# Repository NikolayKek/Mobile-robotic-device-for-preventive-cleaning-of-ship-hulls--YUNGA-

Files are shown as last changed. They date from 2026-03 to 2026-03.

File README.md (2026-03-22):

# Функциональная модель мобильного роботизированного устройства для профилактической чистки судовых корпусов от органических обрастаний «ЮНГА»
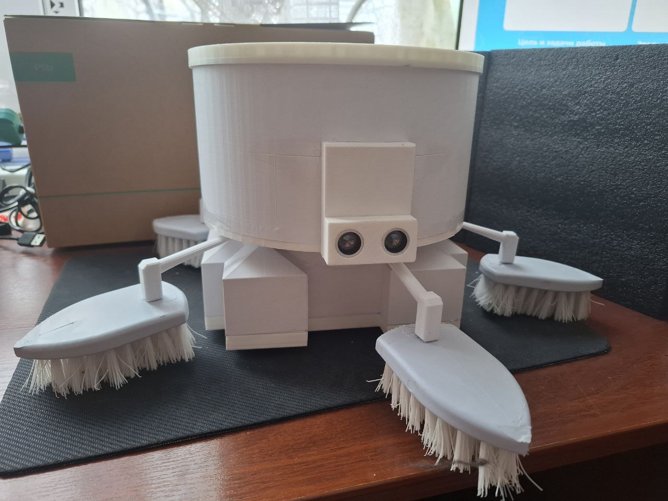
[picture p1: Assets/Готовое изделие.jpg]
Готовое изделие
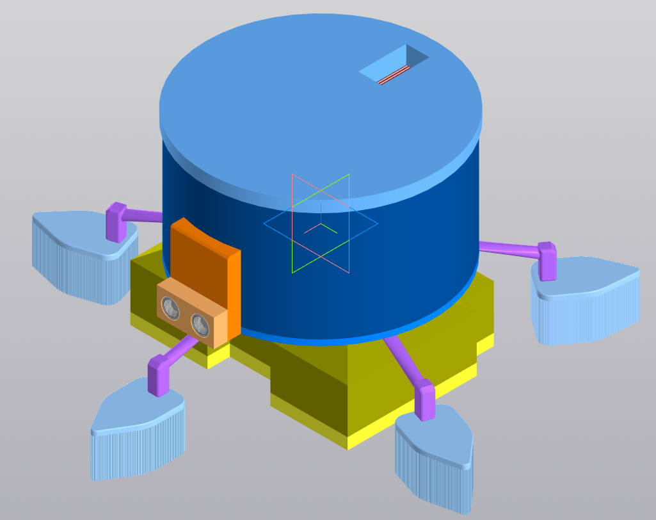
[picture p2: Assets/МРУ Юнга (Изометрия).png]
МРУ Юнга (Изометрия)
  

## Цель создания МРУ Юнга: 
Cпроектировать и изготовить модель мобильного роботизируемого устройства для профилактической чистки корпуса судна от органических обрастаний, без необходимости его постановки в док, которая будет производиться во время стоянки судна или на рейде (на малой скорости или дрейфе) силами экипажа, для оптимизации расходов на содержание судна.

## Задачи проекта: 
- Проанализировать основные методы борьбы с обрастанием  
- Проанализировать типы очистки корпуса корабля  
- Изучить используемые для очистки от обрастаний РУ. 
- Оценить эффективность МРУ.  
- Создать общую концепцию модели. 
- Создать чертеж устройства. 
- Выбрать материалы и комплектующие изделия. 
- Напечатать детали устройства на 3D-принтере. 
- Собрать устройство. 
- Запрограммировать устройство.
- Проверить работу устройства.  

## Общая концепция модели:
Технически МРУ представляет собой мобильную автоматизированную конструкцию, которая крепится на поверхности корпуса судна и перемещается по ней, удаляя грязь и обрастателей. Устройство предназначено для профилактической чистки, которая осуществляется за счет трения щёток о поверхность корпуса судна. 
Электрический двигатель создает и постоянно поддерживает вакуум, за счет которого устройство притягивается корпусу. Одновременно с притяжением происходит перемещение робота по поверхности и удаление загрязнений и прикрепившихся обрастателей. Робот передвигается с помощью треков (гусениц), изготовленных из резины, которые не повреждают поверхность корпуса.  
Питание робота осуществляется при постоянном подключении к электросети судна. Этот метод подачи энергии гарантирует стабильную и бесперебойную работу всех его систем, исключая необходимость в регулярной подзарядке или замене элементов питания. Резервным питанием робота служит аккумулятор. 
МРУ также снабжено стальным страховочным тросом.

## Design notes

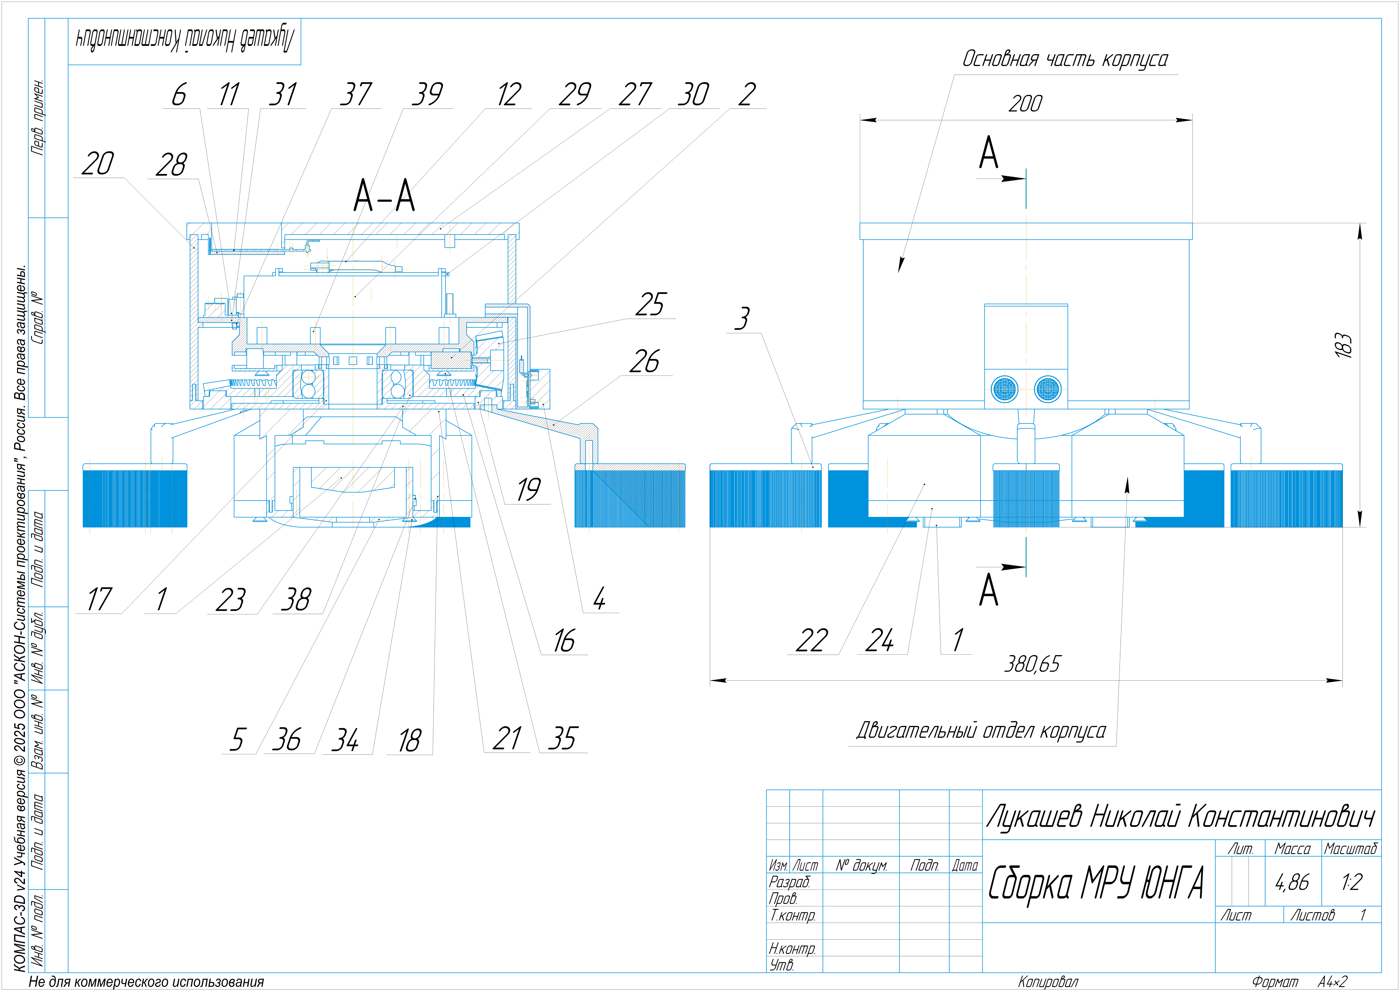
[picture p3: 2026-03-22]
Чертёж, спецификация и приложения/Чертёж сборки/Чертёж сборки МРУ.png

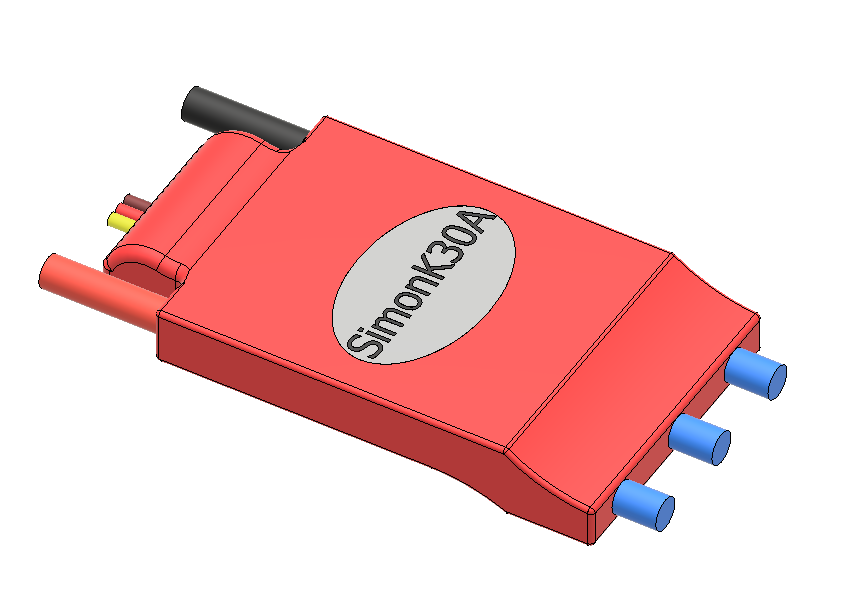
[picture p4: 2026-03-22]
3D модели/В. детали/Для ESC регулятора 30A с прошивкой SimonK/SimonK30A.png

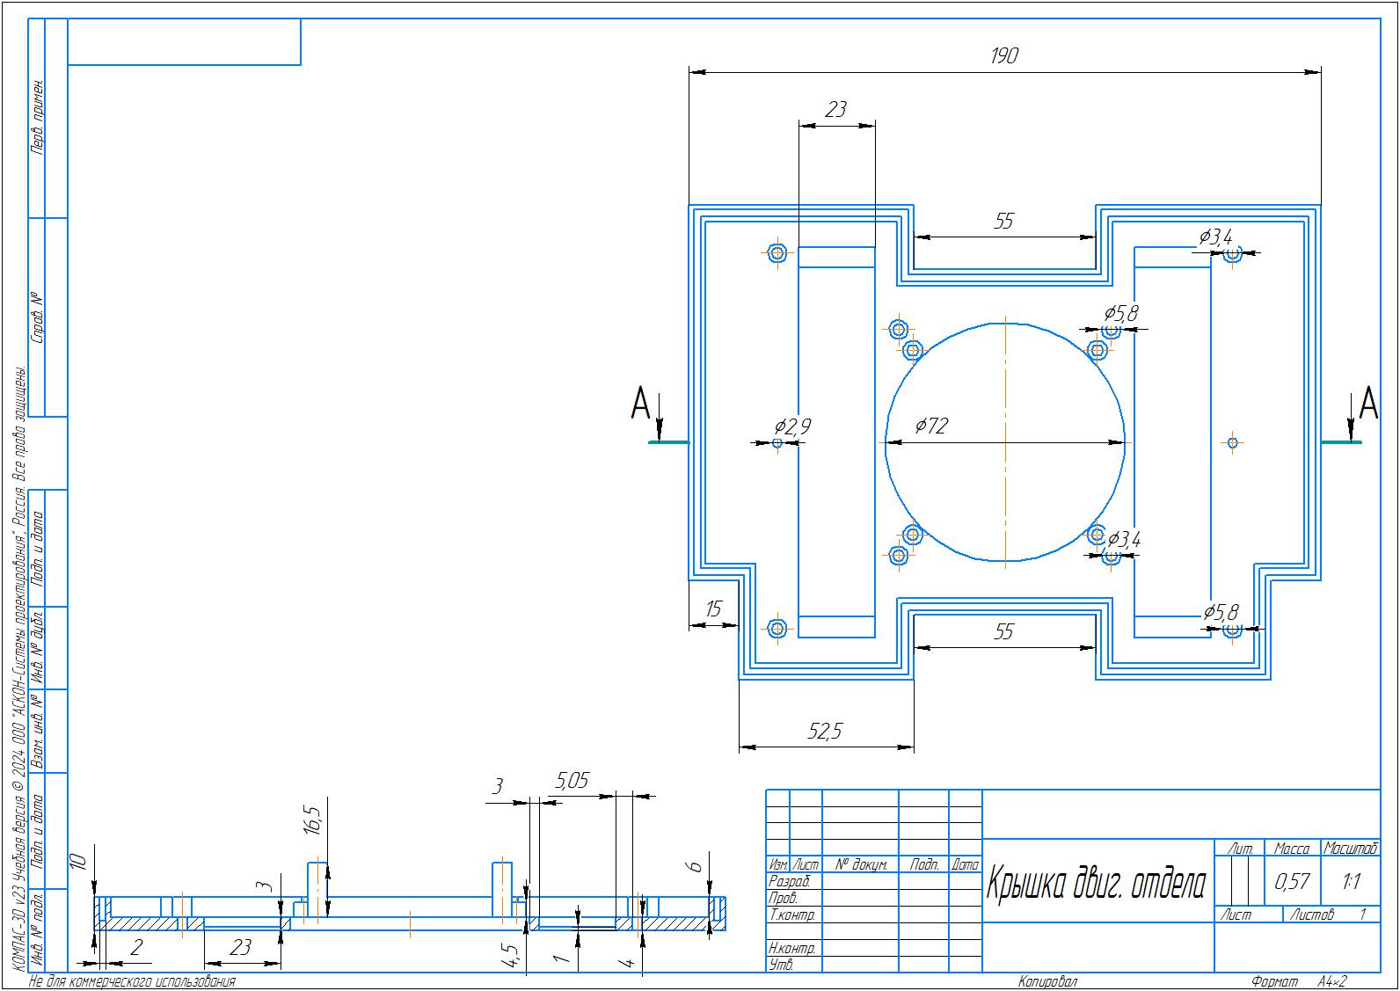
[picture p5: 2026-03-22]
3D модели/Двигательный отдел/Изображения/Крышка двиг. отдела.jpg

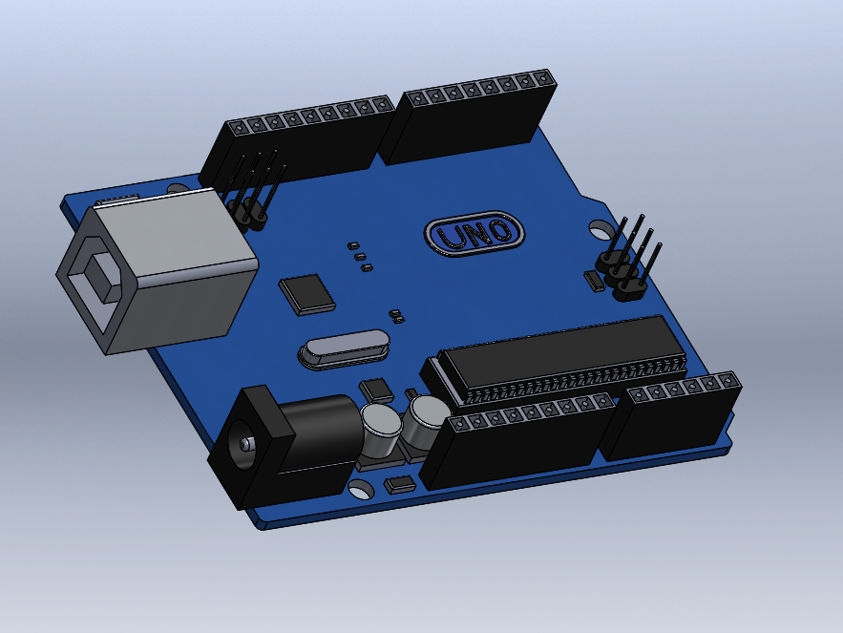
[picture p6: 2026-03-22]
3D модели/В. детали/Для Arduino Uno R3/Arduino Uno R3.PNG

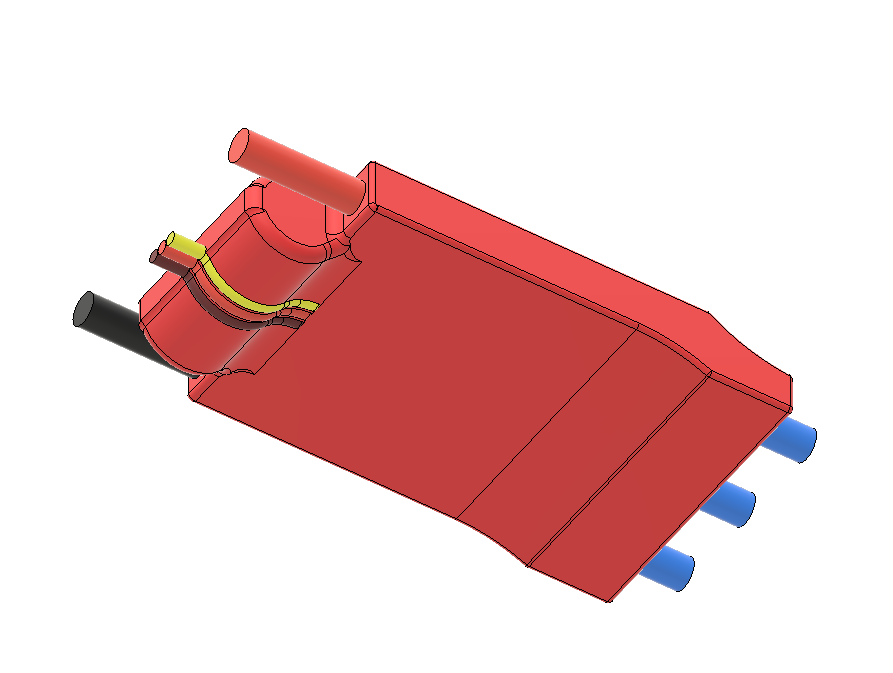
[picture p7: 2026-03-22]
3D модели/В. детали/Для ESC регулятора 30A с прошивкой SimonK/SimonK30A 3.png

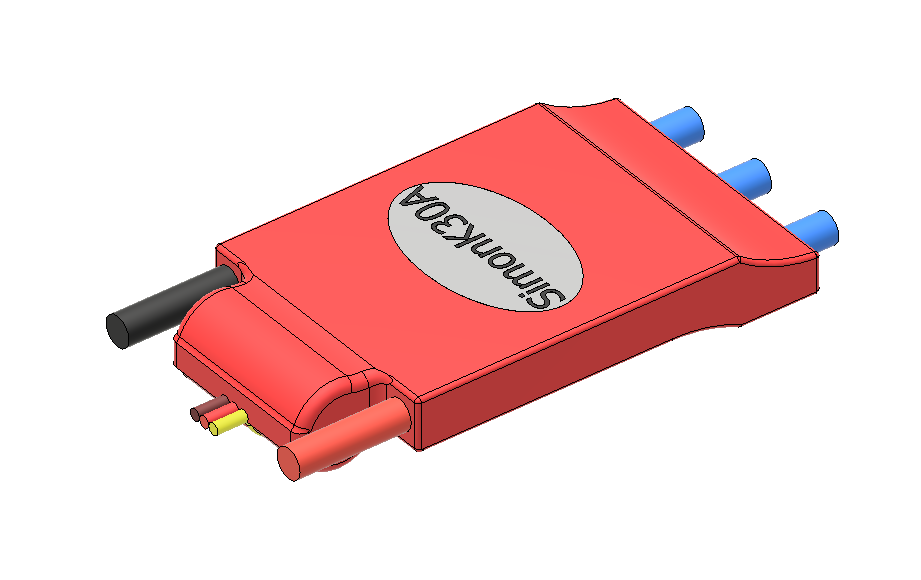
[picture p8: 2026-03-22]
3D модели/В. детали/Для ESC регулятора 30A с прошивкой SimonK/SimonK30A 2.png

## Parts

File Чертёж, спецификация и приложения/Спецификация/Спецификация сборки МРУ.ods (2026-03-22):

Формат | Зона | Поз. | Обозначение | Наименование | Кол. | Приме- чание | Масса | БЦО | Обозн_СТ | Вид изделия | ID ФГ | ID PartLib | Код ОКП | ID материала | Обозначение материала
 |  |  |  | Сборочные единицы
 |  | 1 | $|-$|01$|$|$|$| | Двигатель R-385-18915-3 24V | 2 |  | 0.06
 |  | 2 |  | Мотор - редуктор N20 6V | 3 |  | 0.015
 |  | 3 |  | Щётка | 5 |  | 0.1
 |  | 4 |  | Модуль ультразвукового датчика | 1 |  | 0.028306
 |  | 5 |  | Вакуумный двигатель BL2717 | 1 |  | 0.18
 |  | 6 |  | DC-DC XL6009 | 1 |  | 0.015
 |  | 7 |  | ARDUINO UNO R3 | 1 |  | 0.025
 |  | 8 |  | Aleaivy 3S2P 18650 12В 7000мАч | 1 |  | 0.45
 |  | 9 |  | Amperka Troyka Shield | 1 |  | 0.012
 |  | 10 |  | Amperka Motor Shield L298P | 1 |  | 0.015
 |  | 11 |  | Датчик уровня воды | 1 |  | 0.003
 |  | 12 |  | 30A ESC SimonK Firmware | 1 |  | 0.045
 |  | 13 |  | Реле TRU-5VDC | 1 |  | 0.025
 |  |  |  | Детали
 |  | 16 |  | Шестерня ведомая | 1 |  | 0.107621
 |  | 17 |  | Втулка для подшипника | 1 |  | 0.008976
 |  | 18 |  | Рама для моторов | 1 |  | 0.04811
 |  | 19 |  | Держатель стержней щёток | 1 |  | 0.07984
 |  | 20 |  | Корпус МРУ | 1 |  | 0.276945
 |  | 21 |  | Нижние пазы основной части корпуса МРУ | 1 |  | 0.034244
 |  | 22 |  | Корпус двигательного отдела | 1 |  | 0.282968
 |  | 23 |  | Нижняя часть рамы | 1 |  | 0.050972
@100~) |  | 24 |  | Крышка двигательного отдела | 1 | @100~)A4@4~2 | 0.072419
 |  | 25 |  | Шестерня ведущая | 3 |  | 0.010107
 |  | 26 |  | Стержень для щётки | 5 |  | 0.004759
 |  | 27 |  | Крышка основной части корпуса | 1 |  | 0.223097
 |  | 28 |  | Крышка для датчика воды | 1 |  | 0.002565
 |  | 29 |  | Кейс для аккумуляторный батареи | 1 |  | 0.02469
 |  | 30 |  | Крышка для кейса для аккумуляторной батареи | 1 |  | 0.013936
 |  | 31 |  | Верхняя часть рамы | 1 |  | 0.154037
 |  |  |  | Стандартные изделия
 |  | 34 |  | Countersunk flat head screw ISO 7046-1 - М4 x 20 - H | 6 |  | 0.002 |  |  |  |  | BOSimple***PART:4a2be23b-1094-c2ab-9109-1eb2c62276f1***SHORTLOC:A259_B079D7FF98134C2D[H;0,7;20;4;-;Undefined] |  |  | Сталь 10 ГОСТ 1050-2013
 |  | 35 |  | Countersunk flat head screw ISO 7046-1 - М4 x 25 - Z | 8 |  | 0.00239 |  |  |  |  | BOSimple***PART:92ec0e0d-68d0-4f9e-eaa2-c9b13db8eb2e***SHORTLOC:A259_B079D7FF98134C2D[Z;0,7;25;4;-;Undefined] |  |  | Сталь 10 ГОСТ 1050-2013
 |  | 36 |  | Hexagon thin nut ISO 4035 - М4 | 4 |  | 0.000561 |  |  |  |  | BOSimple***PART:b6312abf-3635-9e75-d080-44536a865479***SHORTLOC:A259_4C5EF5FF3D3C4192[0,7;4;7;-;Undefined] |  |  | Сталь 10 ГОСТ 1050-88
 |  | 37 |  | Винт 2-3x1x10.12 ГОСТ 10619-80 | 4 |  | 0.00046 |  |  |  |  | BOSimple***PART:a135eb40-4c64-62b3-542c-7c3df5bf31bf***SHORTLOC:A86A9_F1ECDF2721C54B79[Нет;Без покрытия;3;10;1;Сталь 30ХГСА ГОСТ 4543-2016] |  | BOSimple***Material:a0aec22f-052f-4fdd-a19d-c95e78cbd053 | Сталь 30ХГСА ГОСТ 4543-2016
 |  | 38 |  | Подшипник 1207 ГОСТ 28428-90 | 1 |  | 0.323 |  |  |  |  | BOSimple***PART:c0ee8c61-a45f-0a07-f1a0-e0ef849b54f1***SHORTLOC:AFFB_506398E62AE44C9C[35;72;17] |  |  | Сталь 10 ГОСТ 1050-88
 |  | 39 |  | Резьбовая втулка | 10 |  | 0.001234

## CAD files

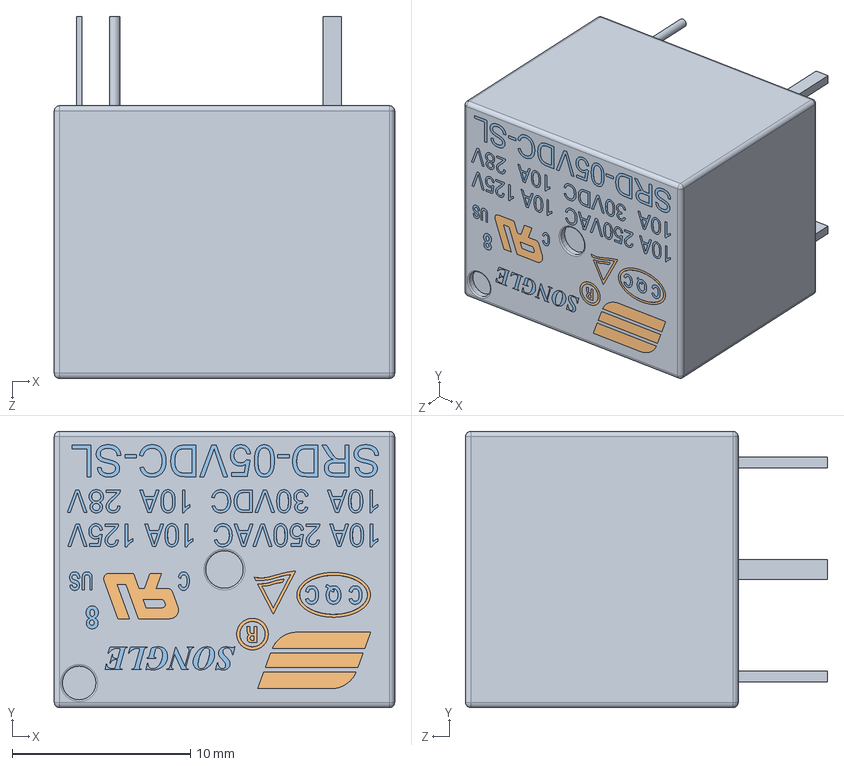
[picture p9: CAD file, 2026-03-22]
3D модели/В. детали/Для реле TRU-5VDC/relay_songle_asm.SLDASM
19.1 x 15.5 x 20.3 mm
Relay SPDT Songle
logos
texts

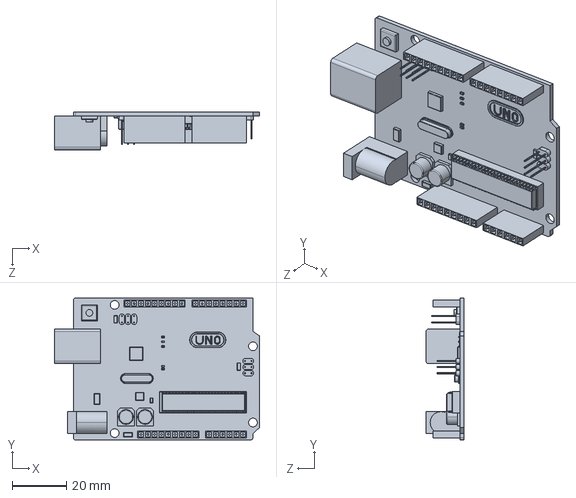
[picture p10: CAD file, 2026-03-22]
3D модели/В. детали/Для Arduino Uno R3/ARDUINO UNO R3 Step.STEP
75.3 x 52.1 x 13.9 mm

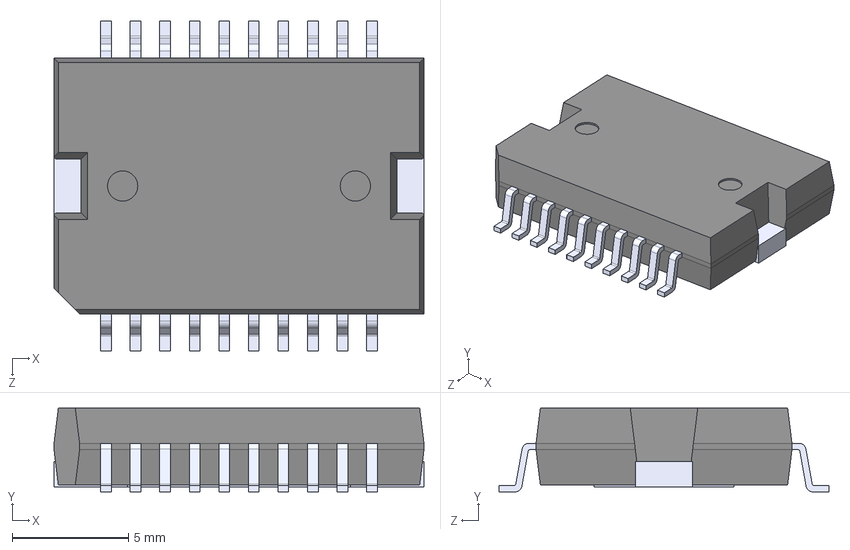
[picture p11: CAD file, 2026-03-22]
3D модели/В. детали/Для драйвера моторов Amperka Motor Shield/L298P_SO20_MODEL.STEP
15.9 x 3.60 x 14.2 mm

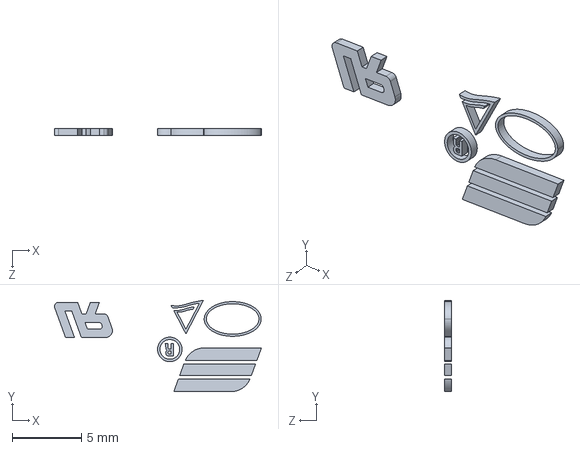
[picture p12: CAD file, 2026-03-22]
3D модели/В. детали/Для реле TRU-5VDC/logos.SLDPRT
15.0 x 6.61 x 0.5 mm

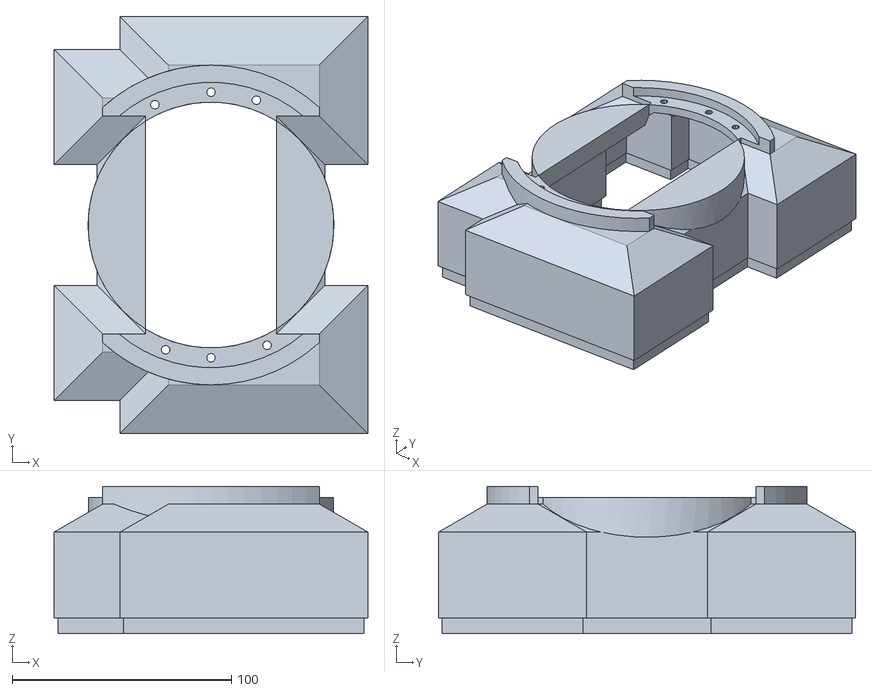
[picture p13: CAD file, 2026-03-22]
3D модели/Двигательный отдел/STL/Корпус двигательного отдела.stl
143.0 x 190.0 x 67.0

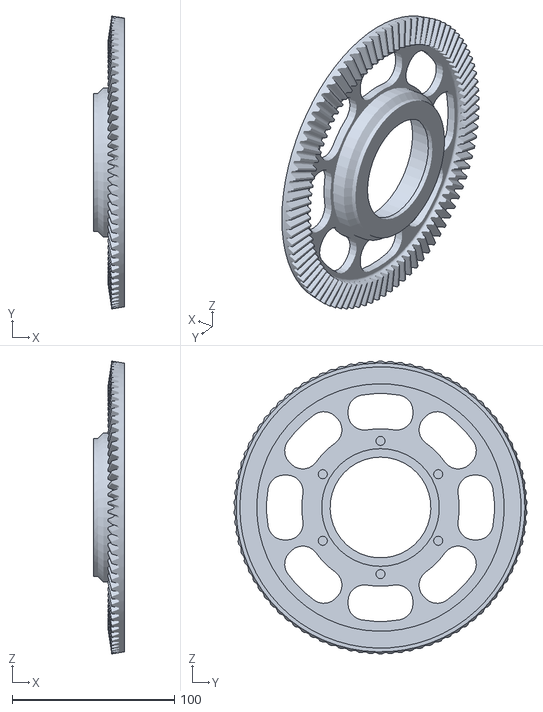
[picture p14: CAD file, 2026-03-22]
3D модели/Модуль отчистки МРУ/STL/Шестерня ведомая.stl
18.9 x 180.3 x 180.3

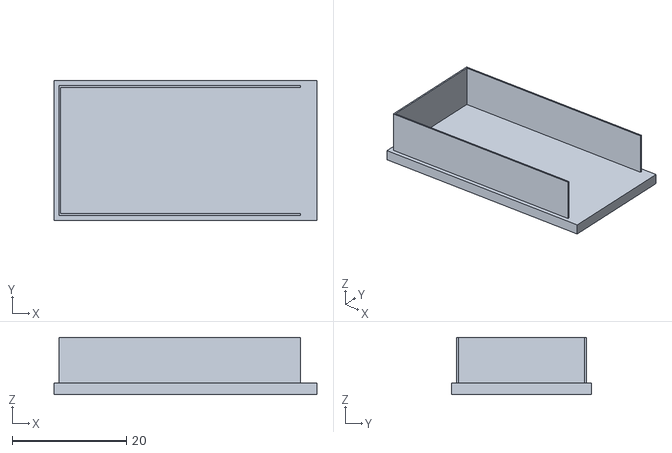
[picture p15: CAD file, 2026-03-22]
3D модели/Основной корпус/STL/Крышка для датчика воды.stl
46.0 x 24.4 x 10.0

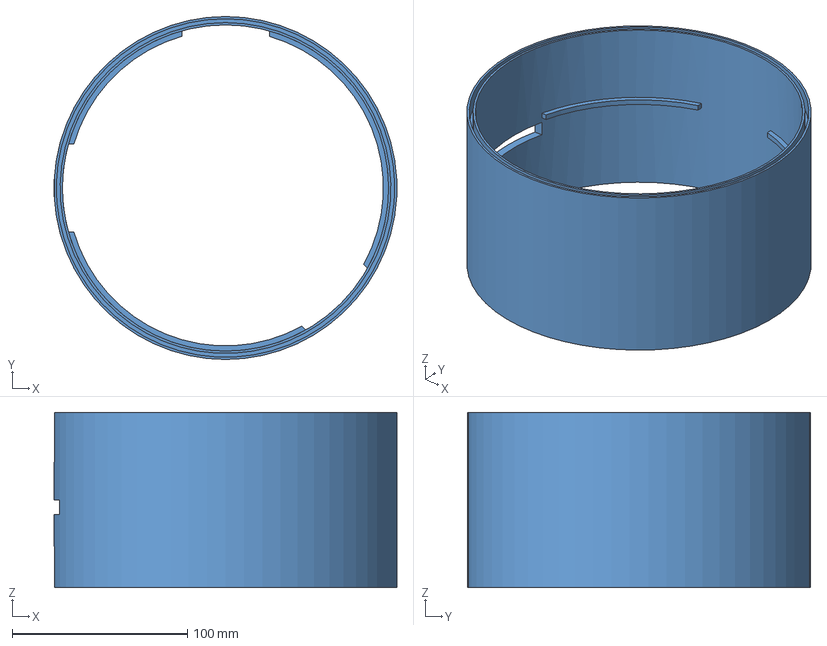
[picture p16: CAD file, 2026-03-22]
3D модели/Основной корпус/Корпус МРУ.stp
195.7 x 196.0 x 100.0 mm

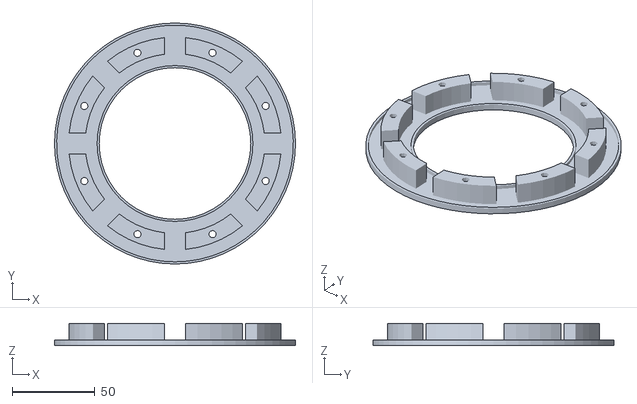
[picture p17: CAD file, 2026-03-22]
3D модели/Рама/STL/Рама для моторов.stl
145.5 x 145.5 x 13.5

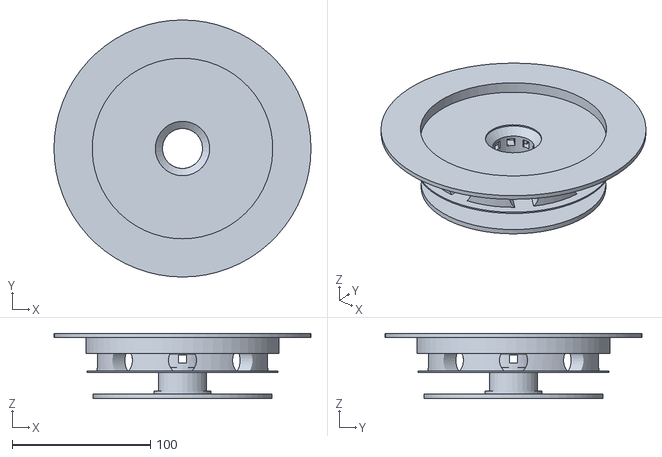
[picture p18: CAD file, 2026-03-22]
3D модели/Рама/Сборка рамы.stl
186.0 x 186.0 x 47.2

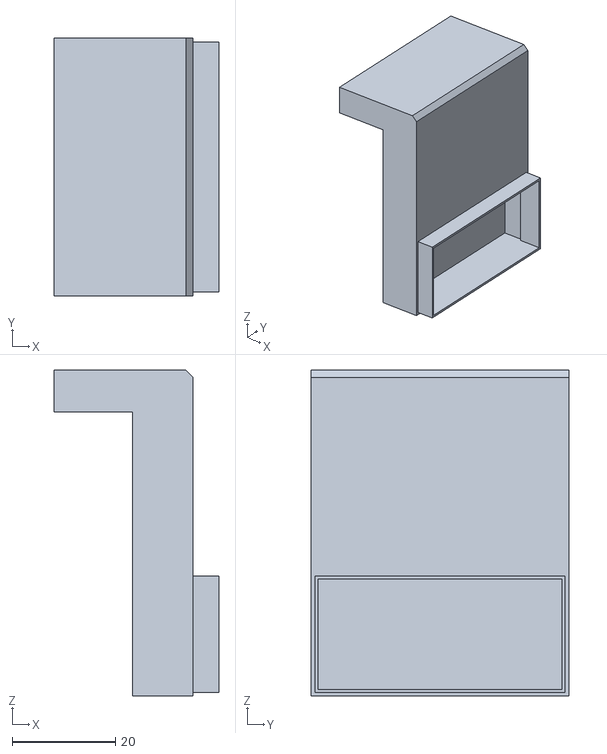
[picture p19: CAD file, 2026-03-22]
3D модели/Ультразвуковой датчик/STL/Мост маска - корпус МРУ.stl
32.0 x 50.0 x 63.3

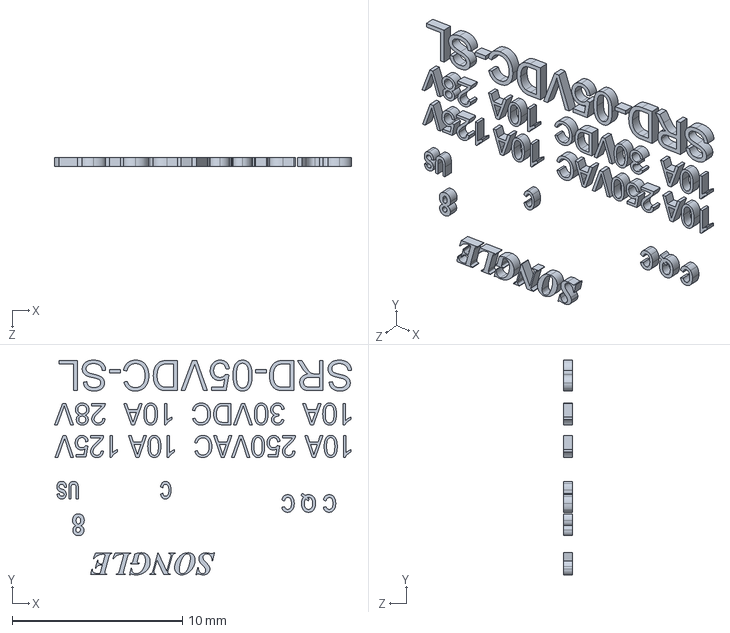
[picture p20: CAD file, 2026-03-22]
3D модели/В. детали/Для реле TRU-5VDC/texts.SLDPRT
17.5 x 12.6 x 0.5 mm

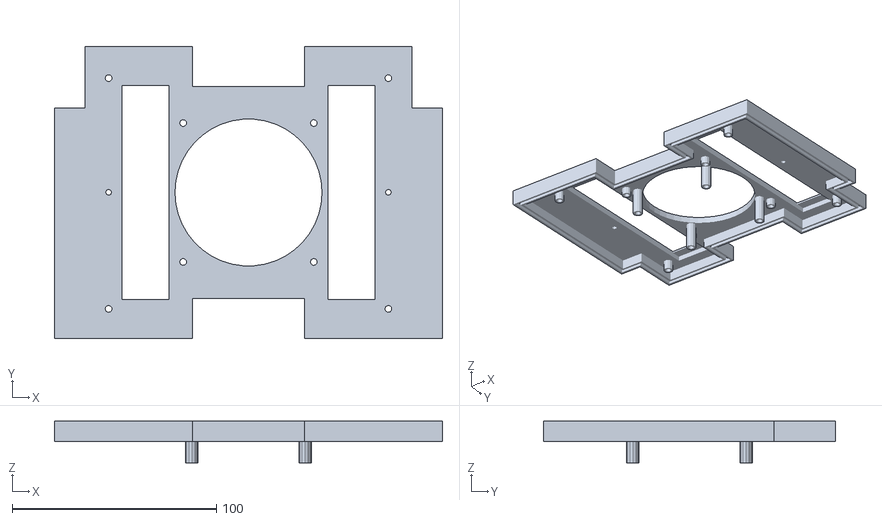
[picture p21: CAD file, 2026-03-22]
3D модели/Двигательный отдел/STL/Крышка двигательного отдела.stl
190.0 x 143.0 x 20.5

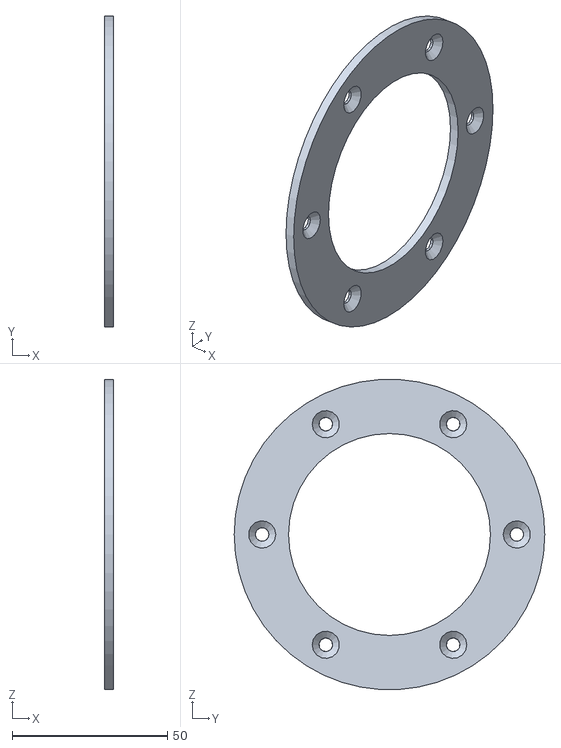
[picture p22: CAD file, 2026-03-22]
3D модели/Модуль отчистки МРУ/STL/Диск.stl
3.00 x 100.0 x 99.8

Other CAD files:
3D модели/Ультразвуковой датчик/Для ультрозвук. датчика.stp
3D модели/В. детали/Для Arduino Uno R3/ARDUINO UNO R3.SLDPRT
3D модели/Двигательный отдел/STL/Шлак STL/Корпус двиг. отдела 2.stl
3D модели/Основной корпус/STL/Крышка основной части корпуса.stl
3D модели/В. детали/Для ESC регулятора 30A с прошивкой SimonK/30A ESC SimonK Firmware.ipt
3D модели/В. детали/Для реле TRU-5VDC/Relay_SPDT_Songle.SLDPRT
3D модели/В. детали/Для реле TRU-5VDC/Relay_SPDT_Songle.STL
3D модели/В. детали/Для реле TRU-5VDC/relay_songle_asm.STL
3D модели/Двигательный отдел/STL/Шлак STL/Корпус двиг. отдела 2 (2).stl
3D модели/Двигательный отдел/STL/Шлак STL/Крышка двиг. отдела 2 V21.stl
3D модели/Двигательный отдел/STL/Шлак STL/Крышка двиг. отдела 2 Распечатать.stl
3D модели/Двигательный отдел/STL/Шлак STL/Крышка двиг. отдела 2.stl
3D модели/Двигательный отдел/STL/Шлак STL/Крышка двиг. отдела.stl
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

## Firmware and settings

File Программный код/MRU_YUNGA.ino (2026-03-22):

// Определяем пины для управления моторами
#define MOTOR1_DIR 4    // Направление первого мотора
#define MOTOR1_SPEED 5  // Скорость первого мотора (PWM)
#define MOTOR2_SPEED 6  // Скорость второго мотора (PWM)
#define MOTOR2_DIR 7    // Направление второго мотора

const int waterLevel = 333;  // задать собственое значение!

void setup() {
  // Настраиваем пины как выходы
  pinMode(MOTOR1_DIR, OUTPUT);
  pinMode(MOTOR1_SPEED, OUTPUT);
  pinMode(MOTOR2_SPEED, OUTPUT);
  pinMode(MOTOR2_DIR, OUTPUT);
  pinMode(2, OUTPUT);
  Serial.begin(9600);
}

void loop() {
  Serial.println(analogRead(A0));
  delay(100);
  testing();
}
void testing() {
  if (analogRead(A0) >= waterLevel) { 
    digitalWrite(2, 1);  // включаем реле
    stopMotors();
    delay(1000);
    // Пример движения вперед
    moveForward(255);  // Максимальная скорость
    delay(2000);       // Движение вперед в течение 2 секунд

    // Пример движения назад
    moveBackward(255);  // Скорость 200 (из 255)
    delay(2000);        // Движение назад в течение 2 секунд
    // Пример поворота влево
    turnLeft(255);  // Скорость 150 (из 255)
    delay(1000);    // Поворот влево в течение 1 секунды

    // Пример поворота вправо
    turnRight(255);  // Скорость 150 (из 255)
    delay(1000);     // Поворот вправо в течение 1 секунды
  } else {
    stopMotors();
    digitalWrite(2, 0);
  }
}
// Функция для движения вперед
void moveForward(int speed) {
  // Первый мотор: направление вперед
  digitalWrite(MOTOR1_DIR, HIGH);
  analogWrite(MOTOR1_SPEED, speed);  // Устанавливаем скорость

  // Второй мотор: направление вперед
  digitalWrite(MOTOR2_DIR, HIGH);
  analogWrite(MOTOR2_SPEED, speed);  // Устанавливаем скорость
}

// Функция для движения назад
void moveBackward(int speed) {
  // Первый мотор: направление назад
  digitalWrite(MOTOR1_DIR, LOW);
  analogWrite(MOTOR1_SPEED, speed);  // Устанавливаем скорость

  // Второй мотор: направление назад
  digitalWrite(MOTOR2_DIR, LOW);
  analogWrite(MOTOR2_SPEED, speed);  // Устанавливаем скорость
}

// Функция для поворота влево
void turnLeft(int speed) {
  // Первый мотор: направление назад
  digitalWrite(MOTOR1_DIR, LOW);
  analogWrite(MOTOR1_SPEED, speed);  // Устанавливаем скорость

  // Второй мотор: направление вперед
  digitalWrite(MOTOR2_DIR, HIGH);
  analogWrite(MOTOR2_SPEED, speed);  // Устанавливаем скорость
}

// Функция для поворота вправо
void turnRight(int speed) {
  // Первый мотор: направление вперед
  digitalWrite(MOTOR1_DIR, HIGH);
  analogWrite(MOTOR1_SPEED, speed);  // Устанавливаем скорость

  // Второй мотор: направление назад
  digitalWrite(MOTOR2_DIR, LOW);
  analogWrite(MOTOR2_SPEED, speed);  // Устанавливаем скорость
}

// Функция для остановки моторов
void stopMotors() {
  // Останавливаем оба мотора (скорость = 0)
  analogWrite(MOTOR1_SPEED, 0);
  analogWrite(MOTOR2_SPEED, 0);
}

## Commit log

2026-03-22 Create МРУ Юнга (Изометрия).png
2026-03-22 Чертёж и спецификация
    [Спецификация сборки МРУ.ods]
2026-03-22 Чертежи и спецификация
2026-03-22 Чертеж с спецификация
2026-03-22 3D модели
2026-03-22 Чертёж м спецификация
2026-03-22 Чертеж, спецификация и приложения
    [Спецификация сборки МРУ.ods]
2026-03-22 Create Готовое изделие.jpg
2026-03-22 экспорт 3D моделей
    [Верхняя часть рамы.stl, Втулка для подшипника.stl, Держатель стержней щёток.stl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]
2026-03-22 Create В. детали - вспомогательные детали.txt
2026-03-22 Amperka Motor Shield L298P
2026-03-23 Переименовка файлов и фиксация деталей с сборке МРУ ЮНГА
